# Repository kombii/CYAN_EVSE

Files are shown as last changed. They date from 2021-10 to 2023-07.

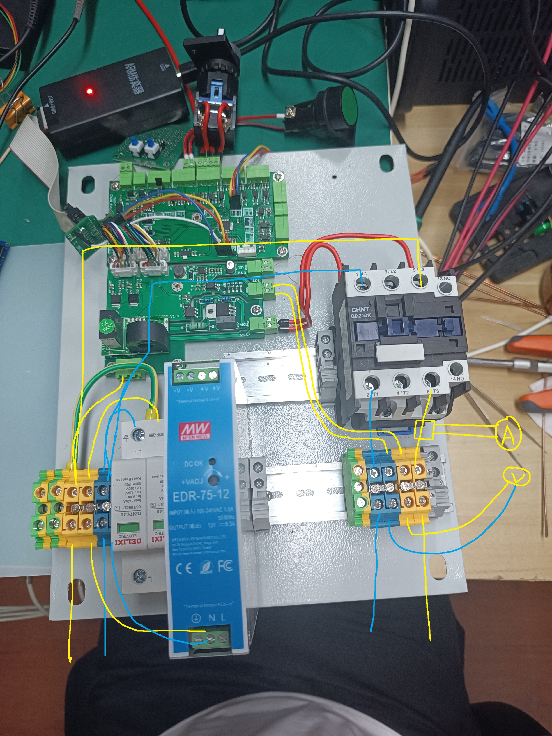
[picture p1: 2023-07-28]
Design/1.2配电 - 副本.jpg

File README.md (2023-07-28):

# CYAN_EVSE
是咱自己的电动小车的充电桩设计。  
## 主要特性
- 符合中国国标GB/T 18487.1-2015
- 按照国标规定的模式3，连接方式C进行设计
- 支持最大32A(7kW)充电模式
- 支持动态供电能力调节
- 过温度断电保护（依赖外部温控开关）
- 电气异常保护（过压、过流、欠压）
- 基于外置电表/计量芯片的准确电能统计
- 完整的保护和工业级组件  
- 支持定时充电，定电量充电
- 可手动指定调节充电电流
- 可实现无感解锁
## 进度  
这是一个进行中的项目，将要实现和完成的功能如下：  
 + 硬件功能
	+ 进行调试测试的原理图绘制✔
	+ 进行测试板的pcb绘制✔
	+ 进行测试板的pcb贴装✔
	+ 进行配电箱的试装✔
	+ 进行发布版本的原理图绘制
	+ 进行发布版本的PCB绘制
	+ 发布完成品
 + 软件功能
	+ 完成PWM和ADC底层驱动✔
	+ 完成电表通信实现✔
	+ 完成充电基础逻辑✔
	+ 完成外部锁定逻辑✔
	+ 完成紧急状态处理逻辑✔
	+ 软件联调和测试✔
## 碎碎念
 已经完成了试运行版本，还缺少定时启动的功能，不得不说有些车企的设计理念和用户需求完全不沾边啊。。。。。

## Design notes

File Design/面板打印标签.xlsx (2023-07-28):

警告 | 急停
市电接入 | 车辆连接 | 鉴权锁定
确定/菜单 | 充电启动 | 选择/±
警告 | 急停
市电接入 | 车辆连接 | 鉴权锁定
确定/菜单 | 充电启动 | 选择/±

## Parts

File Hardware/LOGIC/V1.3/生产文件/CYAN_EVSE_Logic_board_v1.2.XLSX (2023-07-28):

Comment | Designator | Footprint
10K | R1, R4, R5, R6 | 0805 | 4
4.7K | R2, R16, R21, R26, R33, R36, R39, R40, R44, R47 | 0805 | 10
120 | R3 | 1206 | 1
1K | R7, R10, R12, R15, R19, R24, R30 | 0805 | 7
1M | R8, R9, R11, R13, R17, R18, R22, R23, R27, R29, R34, R41, R45, R48 | 0805 | 14
100 | R14, R20, R25, R32, R35, R43, R46 | 0805 | 7
100K | R28, R37 | 0805 | 2
0 | R31, R49 | 0805 | 2
150K | R38 | 0805 | 1
39K | R42 | 0805 | 1
180 | R52 | 0805 | 1
1K | R54 | 1206 | 1
100nF 20V | C1, C2, C3, C4, C5, C8, C9, C12, C13, C16, C17, C18, C19, C20, C21, C22, C23, C25, C26, C27, C28, C30, C31 | 0805 | 23
1uF 20V | C6, C7, C24 | 0805 | 3
22pF 20V | C10, C14 | 0805 | 2
8.2pF 20V | C11, C15 | 0805 | 2
3.3nF 50V | C29 | 1206 | 1
SMBJ16CA | DR1 | SMB | 1
MAX3485 | IC1 | SOP8 | 1
TLP187 | IC2, IC5, IC7, IC8, IC10, IC11, IC12, IC13, IC14, IC15, IC16, IC18, IC19, IC20 | SOP6_4.6MM_W1.27_4PIN_N | 14
TLC372 | IC3 | SOP8 | 1
LMV358 | IC4, IC6 | SOP8 | 2
FOD8314 | IC9 | SOP6_7MM_WIDE_LEAD_N | 1
SI2302 | Q1, Q2, Q3, Q4, Q5 | SOT23-3 | 5
STM/GD32F103C8T6 | U1 | LQFP48 7X7 | 1
AMS1117-3V3 | V1 | SOT223 | 1
1N4148 | VD1, VD3 | SOD323 | 2
SMBJ6.8CA | VD2, VD4 | SMB | 2
8M 无源 | X1 | 3225 | 1
32.768khz 6pF 无源 | X2 | 3215 | 1
M3 | [NoValue], *1, *2, *3, *5 | M3 125X300 | 5
HDR-1X2 | J485R, JP4, JP8 | MC 1,5/ 2-G-3,81 | 3
HDR-1X6 | JP1, JP2 | XH2.54-6P | 2
HDR-1X4 | JP3, JP5, JP6, JP7, JP9, JP10, JP12 | MC 1,5/ 4-G-3,81 | 7
HDR-1X4 | JP11 | XH2.54-4P | 1
HDR-1X5 | JP13 | HDR-1X5 | 1
HDR-1X3 | JP14, JP15, JP16 | HDR-1X3 | 3
DS18B20 | IC17 | TO92A | 1
DEBUG PAD | TP1 | DEBUG PAD2 | 1

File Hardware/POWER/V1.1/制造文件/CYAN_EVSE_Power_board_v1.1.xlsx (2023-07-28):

Comment | Value | Voltage | Designator | Footprint | Quantity
C | 100nF | 25V | C1 | 0805 | 1
C | 100nf | 50V | C2, C3, C6, C15, C17, C19, C21 | 0805 | 7
C | 10uF | 50V | C4, C5, C14, C16, C18, C20 | 0805 | 6
C | 10uF | 25V | C7 | 0805 | 1
C | 10nf | 50V | C8 | 0805 | 1
C | 100nF | 20V | C9, C23 | 0805 | 2
X1 安规电容 | 10nf | 440V | CX2 | CX 10*13*11 | 1
C-CM | 220uf | 20V | E1 | CM D(6.3*5.4) | 1
BTA16_800 |  |  | IC1 | TO220B | 1
MOC3061 |  |  | IC2 | DIP6-300 | 1
PC817 |  |  | IC4 | SOP4-W2.54_M | 1
100uH |  |  | L2 | CD75 | 1
IM1281B |  |  | M2 | IM1281B | 1
S9014 |  |  | Q1 | SOT23-3N | 1
R | 16k |  | R1 | 0805 | 1
R | 1.8k |  | R3 | 0805 | 1
R | 10k |  | R6, R8 | 0805 | 2
R-CRR | 360 |  | R7, R10 | RS 1/2W | 2
R-CRR | 39 |  | R9 | RS 2W | 1
R | 180 |  | R11 | 0805 | 1
R | 51K |  | R13, R14, R15, R16 | 1206 | 4
R | 1M |  | R17 | 0805 | 1
TPS5430 |  |  | U1 | SOP8 | 1
7805 |  |  | V1 | TO252 | 1
7905 |  |  | V2 | TO252 | 1
B340AF-13 |  |  | VD1 | SMA | 1
FR107 |  |  | VD2 | SOD-123 | 1
M3 |  |  | *1, *2, *3, *5, *7 | M3 125X300 | 5
HDR-1X3 |  |  | JACIN | KF2EDGK5.0-3P_H | 1
HDR-1X2 |  |  | JACOUT, JDCIN, JMCOUT | MC 1,5/ 2-G-3,81 | 3
HDR-1X6 |  |  | JP1, JP2 | XH2.54-6P | 2

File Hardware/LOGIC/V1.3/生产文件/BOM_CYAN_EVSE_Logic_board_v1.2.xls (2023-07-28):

客户BOM清单 |  |  |  | 嘉立创用料信息
 |  |  |  | 匹配类型 | 匹配方式 | 匹配来源 | 顶层位号 | 顶层数 | 顶层贴装 | 底层位号 | 底层数 | 底层贴装 | 元件编号 | X-ray检查 | 贴装总数量 | 焊点总数量 | 焊点费小计 | 库类型 | 组装方式 | 元件名称 | 封装规格 | 最小起订数量 | 损耗数量 | 元器件来源 | 使用预订数量 | 工厂提供数量 | 工厂元件单价 | 工厂元件小计 | 收费原因
100nF20V | C1,C2,C3,C4,C5,C8,C9,C12,C13,C16,C17,C18,C19,C20,C21,C22,C23,C25,C26,C27,C28,C30,C31 | 0805 | 23 | 手动调整 | 手动替换 |  | C1, C2, C3, C4, C5, C8, C9, C12, C13, C16, C17, C18, C19, C20, C21, C22, C23, C25, C26, C27, C28, C30, C31 | 23 | 已贴装 |  | 0 | 未贴装 | C49678 | 不需要 | 115 | 230 | 2.30 | 基础库 | SMT贴片 | 100nF(104) ±10% 50V X7R | 0805 | 0 | 0 | 立创商城 | 0 | 115 | 0.0287 | 3.3005
150K | R38 | 0805 | 1 | 系统识别 | 自动匹配 |  | R38 | 1 | 已贴装 |  | 0 | 未贴装 | C17470 | 不需要 | 5 | 10 | 0.10 | 基础库 | SMT贴片 | 150KΩ (1503) ±1% | 0805 | 0 | 0 | 立创商城 | 0 | 5 | 0.0143 | 0.0715
1uF20V | C6,C7,C24 | 0805 | 3 | 系统识别 | 自动匹配 |  | C6, C7, C24 | 3 | 已贴装 |  | 0 | 未贴装 | C28323 | 不需要 | 15 | 30 | 0.30 | 基础库 | SMT贴片 | 1uF (105) ±10% 50V X7R | 0805 | 0 | 0 | 立创商城 | 0 | 15 | 0.0578 | 0.8670
SI2302 | Q1,Q2,Q3,Q4,Q5 | SOT23-3 | 5 | 手动调整 | 手动替换 |  | Q1, Q2, Q3, Q4, Q5 | 5 | 已贴装 |  | 0 | 未贴装 | C2891732 | 不需要 | 25 | 75 | 0.75 | 扩展库 | SMT贴片 | SI2302 | SOT-23-3 | 15 | 4 | 立创商城 | 0 | 29 | 0.1310 | 3.7990
4.7K | R2,R16,R21,R26,R33,R36,R39,R40,R44,R47 | 0805 | 10 | 系统识别 | 自动匹配 |  | R2, R16, R21, R26, R33, R36, R39, R40, R44, R47 | 10 | 已贴装 |  | 0 | 未贴装 | C17673 | 不需要 | 50 | 100 | 1.00 | 基础库 | SMT贴片 | 4.7KΩ (4701) ±1% | 0805 | 0 | 0 | 立创商城 | 0 | 50 | 0.0152 | 0.7600
22pF20V | C10,C14 | 0805 | 2 | 手动调整 | 手动替换 |  | C10, C14 | 2 | 已贴装 |  | 0 | 未贴装 | C1804 | 不需要 | 10 | 20 | 0.20 | 基础库 | SMT贴片 | 22pF (220) ±5% 50V C0G | 0805 | 0 | 0 | 立创商城 | 0 | 10 | 0.0708 | 0.7080
1K | R54 | 1206 | 1 | 系统识别 | 自动匹配 |  | R54 | 1 | 已贴装 |  | 0 | 未贴装 | C4410 | 不需要 | 5 | 10 | 0.10 | 基础库 | SMT贴片 | 1KΩ (1001) ±1% | 1206 | 0 | 0 | 立创商城 | 0 | 5 | 0.0238 | 0.1190
0 | R31,R49 | 0805 | 2 | 系统识别 | 自动匹配 |  | R31, R49 | 2 | 已贴装 |  | 0 | 未贴装 | C17477 | 不需要 | 10 | 20 | 0.20 | 基础库 | SMT贴片 | 0Ω (0R0) ±1% | 0805 | 0 | 0 | 立创商城 | 0 | 10 | 0.0138 | 0.1380
180 | R52 | 0805 | 1 | 系统识别 | 自动匹配 |  | R52 | 1 | 已贴装 |  | 0 | 未贴装 | C25270 | 不需要 | 5 | 10 | 0.10 | 基础库 | SMT贴片 | 180Ω (1800) ±1% | 0805 | 0 | 0 | 立创商城 | 0 | 5 | 0.0139 | 0.0695
10K | R1,R4,R5,R6 | 0805 | 4 | 系统识别 | 自动匹配 |  | R1, R4, R5, R6 | 4 | 已贴装 |  | 0 | 未贴装 | C17414 | 不需要 | 20 | 40 | 0.40 | 基础库 | SMT贴片 | 10KΩ (1002) ±1% | 0805 | 0 | 0 | 立创商城 | 0 | 20 | 0.0127 | 0.2540
1K | R7,R10,R12,R15,R19,R24,R30 | 0805 | 7 | 系统识别 | 自动匹配 |  | R7, R10, R12, R15, R19, R24, R30 | 7 | 已贴装 |  | 0 | 未贴装 | C17513 | 不需要 | 35 | 70 | 0.70 | 基础库 | SMT贴片 | 1KΩ (1001) ±1% | 0805 | 0 | 0 | 立创商城 | 0 | 35 | 0.0132 | 0.4620
1N4148 | VD1,VD3 | SOD323 | 2 | 系统识别 | 自动匹配 |  | VD1, VD3 | 2 | 已贴装 |  | 0 | 未贴装 | C2128 | 不需要 | 10 | 20 | 0.20 | 基础库 | SMT贴片 | 1N4148 | SOD-323F | 0 | 0 | 立创商城 | 0 | 10 | 0.0889 | 0.8890
1M | R8,R9,R11,R13,R17,R18,R22,R23,R27,R29,R34,R41,R45,R48 | 0805 | 14 | 手动调整 | 手动替换 |  | R8, R9, R11, R13, R17, R18, R22, R23, R27, R29, R34, R41, R45, R48 | 14 | 已贴装 |  | 0 | 未贴装 | C17514 | 不需要 | 70 | 140 | 1.40 | 基础库 | SMT贴片 | 1MΩ (1004) ±1% | 0805 | 0 | 0 | 立创商城 | 0 | 70 | 0.0139 | 0.9730
100K | R28,R37 | 0805 | 2 | 系统识别 | 自动匹配 |  | R28, R37 | 2 | 已贴装 |  | 0 | 未贴装 | C17407 | 不需要 | 10 | 20 | 0.20 | 基础库 | SMT贴片 | 100KΩ (1003) ±1%【停用，变更为C149504】 | 0805 | 0 | 0 | 立创商城 | 0 | 10 | 0.0144 | 0.1440
100 | R14,R20,R25,R32,R35,R43,R46 | 0805 | 7 | 系统识别 | 自动匹配 |  | R14, R20, R25, R32, R35, R43, R46 | 7 | 已贴装 |  | 0 | 未贴装 | C17408 | 不需要 | 35 | 70 | 0.70 | 基础库 | SMT贴片 | 100Ω (1000) ±1% | 0805 | 0 | 0 | 立创商城 | 0 | 35 | 0.0164 | 0.5740
AMS1117-3V3 | V1 | SOT223 | 1 | 系统识别 | 自动匹配 |  | V1 | 1 | 已贴装 |  | 0 | 未贴装 | C6186 | 不需要 | 5 | 20 | 0.20 | 基础库 | SMT贴片 | AMS1117-3.3 | SOT-223 | 0 | 0 | 立创商城 | 0 | 5 | 1.0711 | 5.3555
120 | R3 | 1206 | 1 | 系统识别 | 自动匹配 |  | R3 | 1 | 已贴装 |  | 0 | 未贴装 | C17909 | 不需要 | 5 | 10 | 0.10 | 基础库 | SMT贴片 | 120Ω(1200) ±1% | 1206 | 0 | 0 | 立创商城 | 0 | 5 | 0.0241 | 0.1205
39K | R42 | 0805 | 1 | 系统识别 | 自动匹配 |  | R42 | 1 | 已贴装 |  | 0 | 未贴装 | C25826 | 不需要 | 5 | 10 | 0.10 | 基础库 | SMT贴片 | 39KΩ (3902) ±1% | 0805 | 0 | 0 | 立创商城 | 0 | 5 | 0.0140 | 0.0700
<-以下为不贴装的元件->
LMV358 | IC4,IC6 | SOP8 | 2
SMBJ6.8CA | VD2,VD4 | SMB | 2
3.3nF50V | C29 | 1206 | 1
MAX3485 | IC1 | SOP8 | 1
8.2pF20V | C11,C15 | 0805 | 2
FOD8314 | IC9 | SOP6_7MM_WIDE_LEAD_N | 1
TLC372 | IC3 | SOP8 | 1
TLP187 | IC2,IC5,IC7,IC8,IC10,IC11,IC12,IC13,IC14,IC15,IC16,IC18,IC19,IC20 | SOP6_4.6MM_W1.27_4PIN_N | 14
SMBJ16CA | DR1 | SMB | 1
STM/GD32F103C8T6 | U1 | LQFP487X7 | 1
32.768khz6pF无源 | X2 | 3215 | 1
8M无源 | X1 | 3225 | 1
HDR-1X6 | JP1,JP2 | XH2.54-6P | 2
M3 | [NOVALUE],*1,*2,*3,*5 | M3125X300 | 5
HDR-1X3 | JP14,JP15,JP16 | HDR-1X3 | 3
HDR-1X5 | JP13 | HDR-1X5 | 1
HDR-1X4 | JP3,JP5,JP6,JP7,JP9,JP10,JP12 | HDR-1X4 | 7
HDR-1X2 | J485R,JP4,JP8 | MC1,5/2-G-3,81 | 3
HDR-1X4 | JP11 | HDR-1X4 | 1
DEBUGPAD | TP1 | DEBUGPAD2 | 1
DS18B20 | IC17 | TO92A | 1

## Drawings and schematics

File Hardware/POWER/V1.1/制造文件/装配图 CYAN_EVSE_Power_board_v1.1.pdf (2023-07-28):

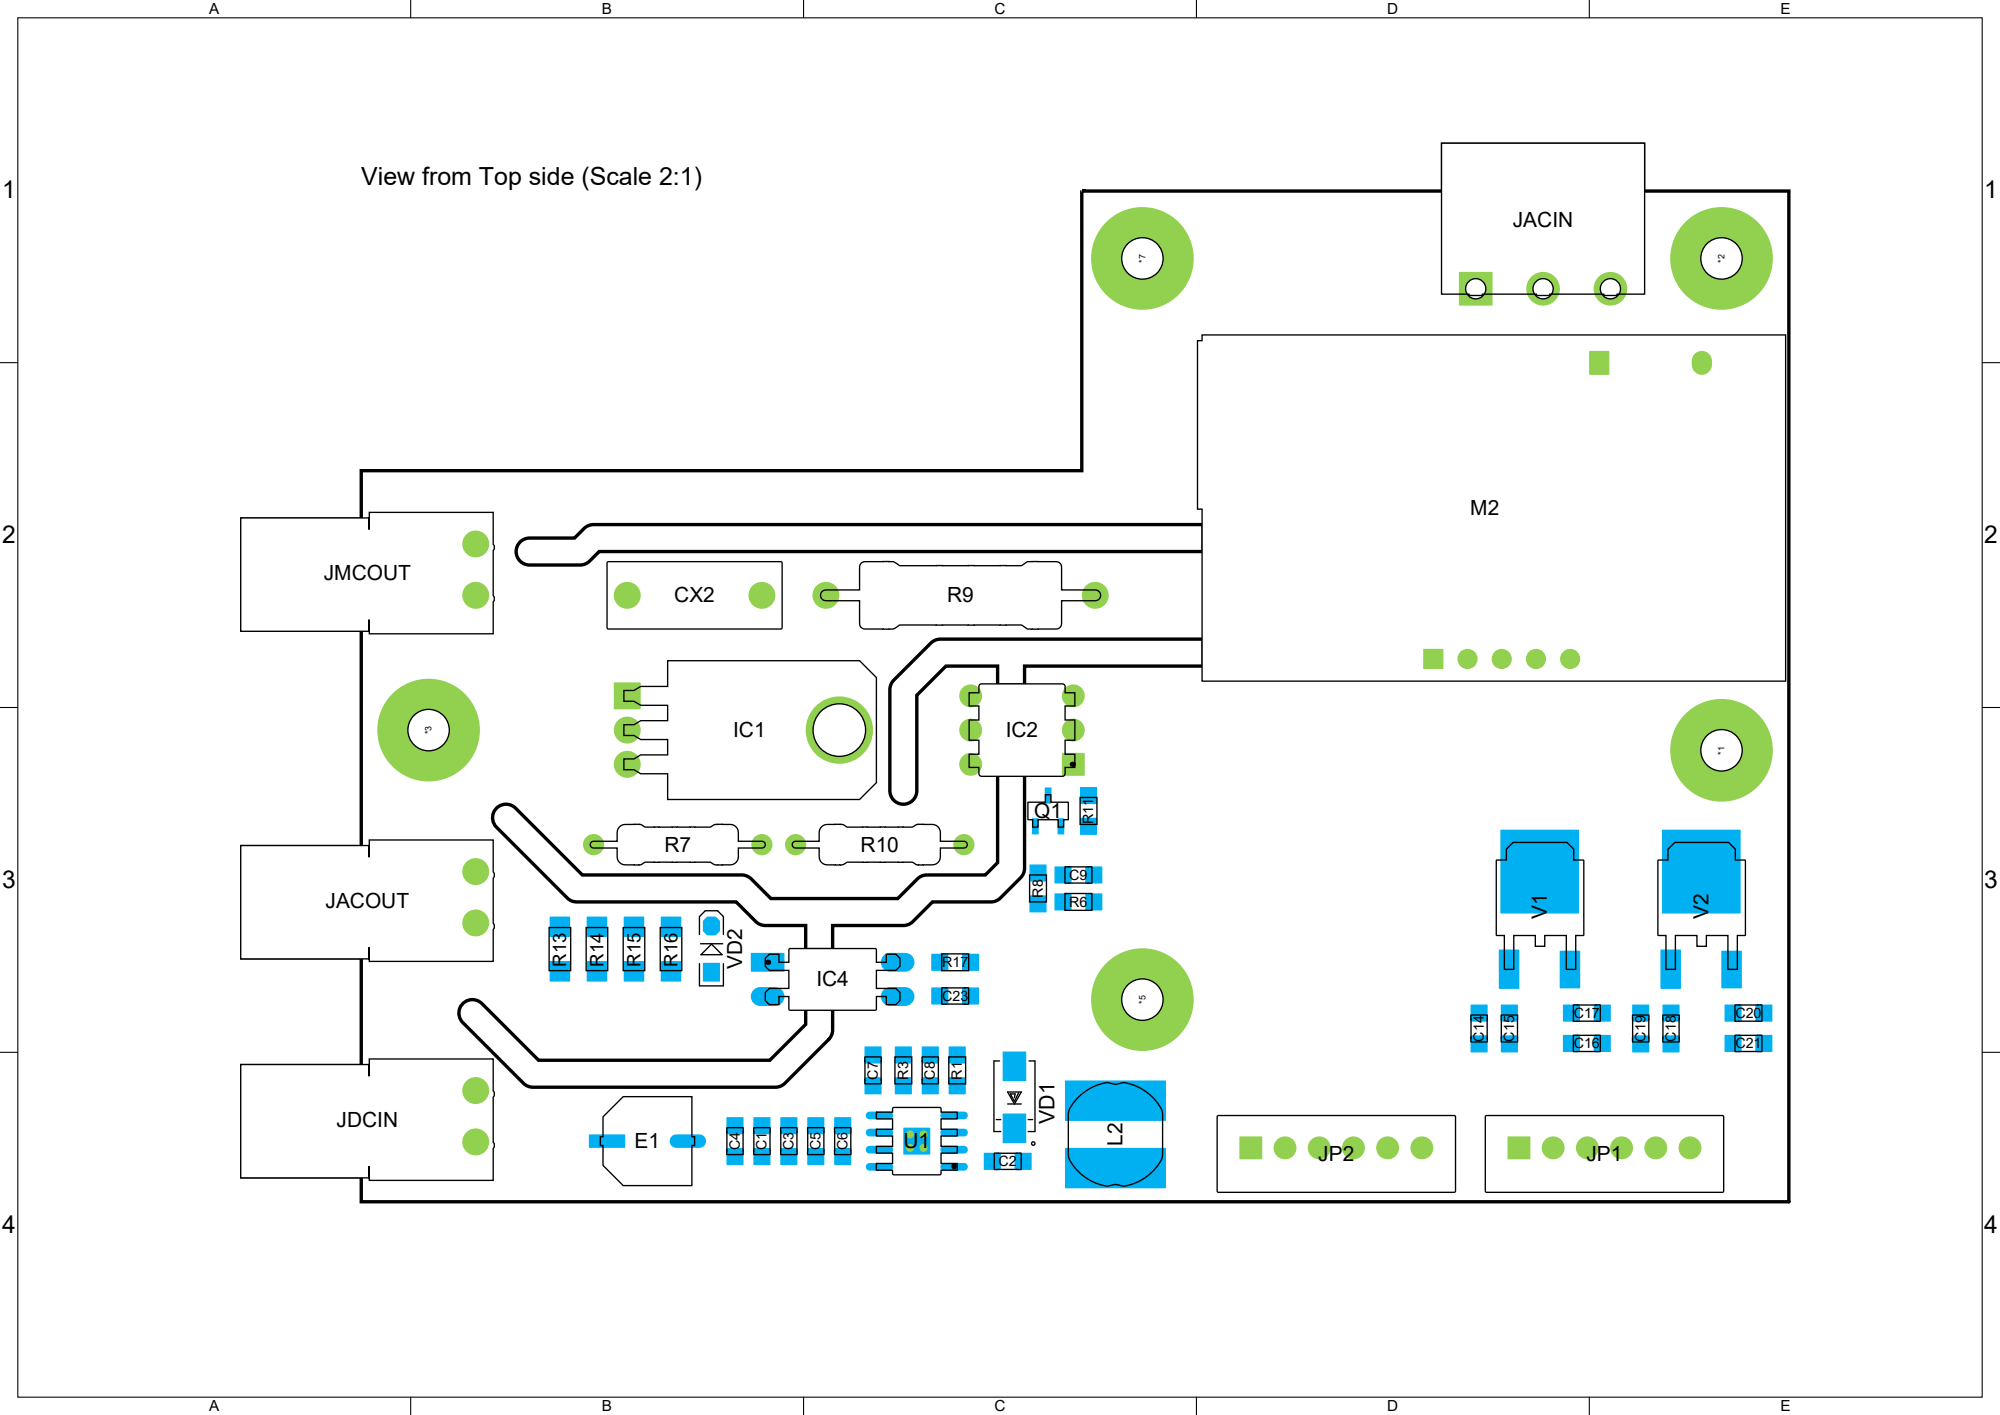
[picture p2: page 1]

View from Top side (Scale 2:1)

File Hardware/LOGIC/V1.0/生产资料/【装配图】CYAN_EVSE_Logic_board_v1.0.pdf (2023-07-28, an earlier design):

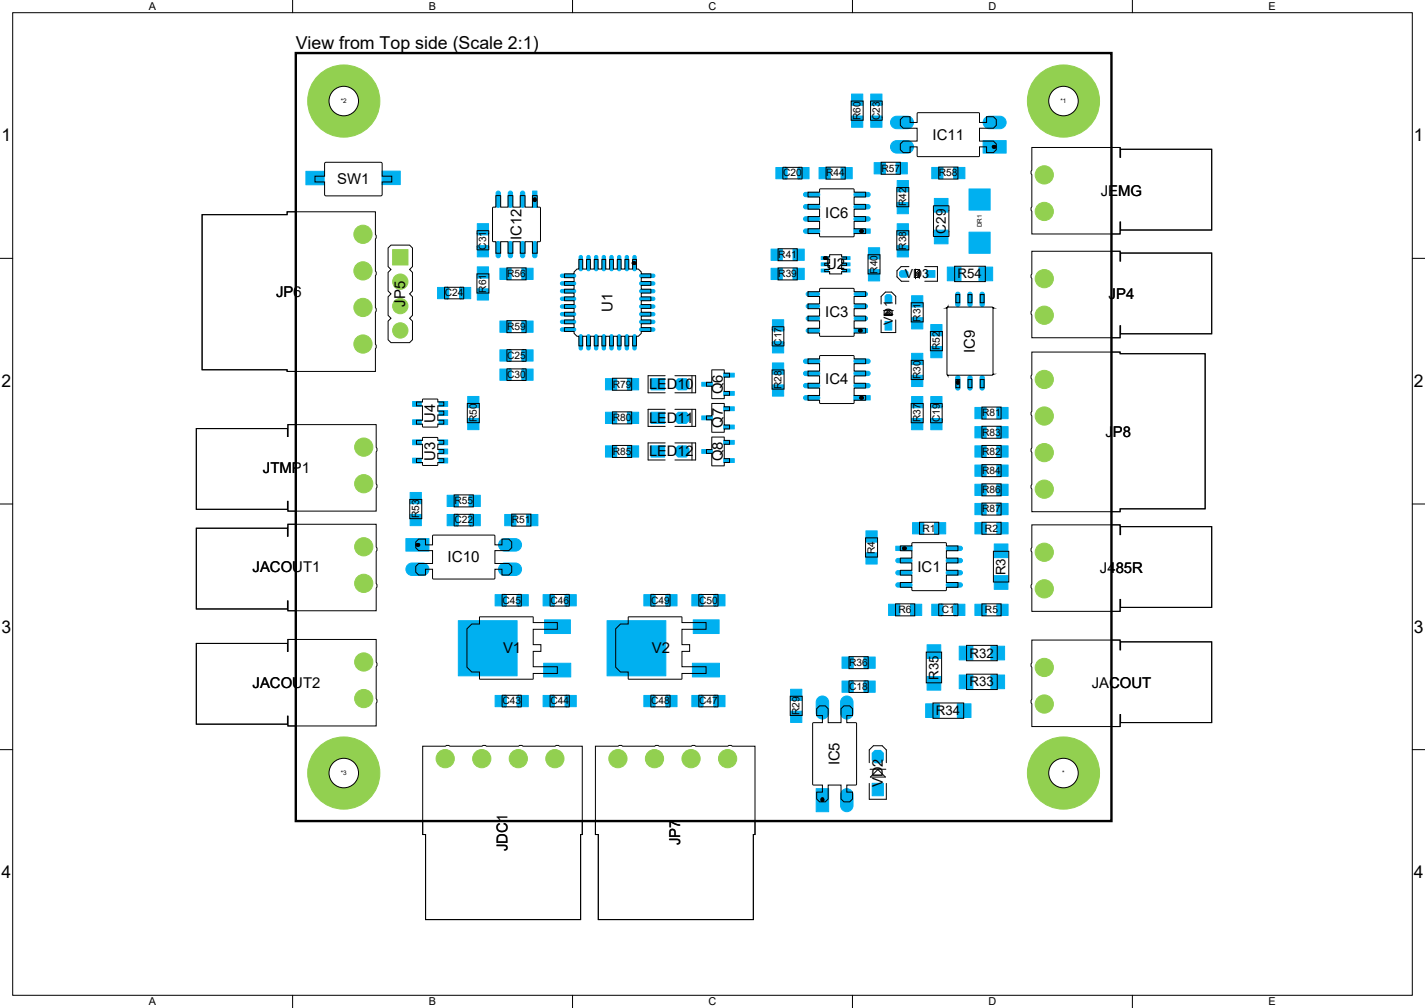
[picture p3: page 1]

View from Top side (Scale 2:1)

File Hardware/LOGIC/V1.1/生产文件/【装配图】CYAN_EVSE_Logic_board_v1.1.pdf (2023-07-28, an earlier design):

A

B

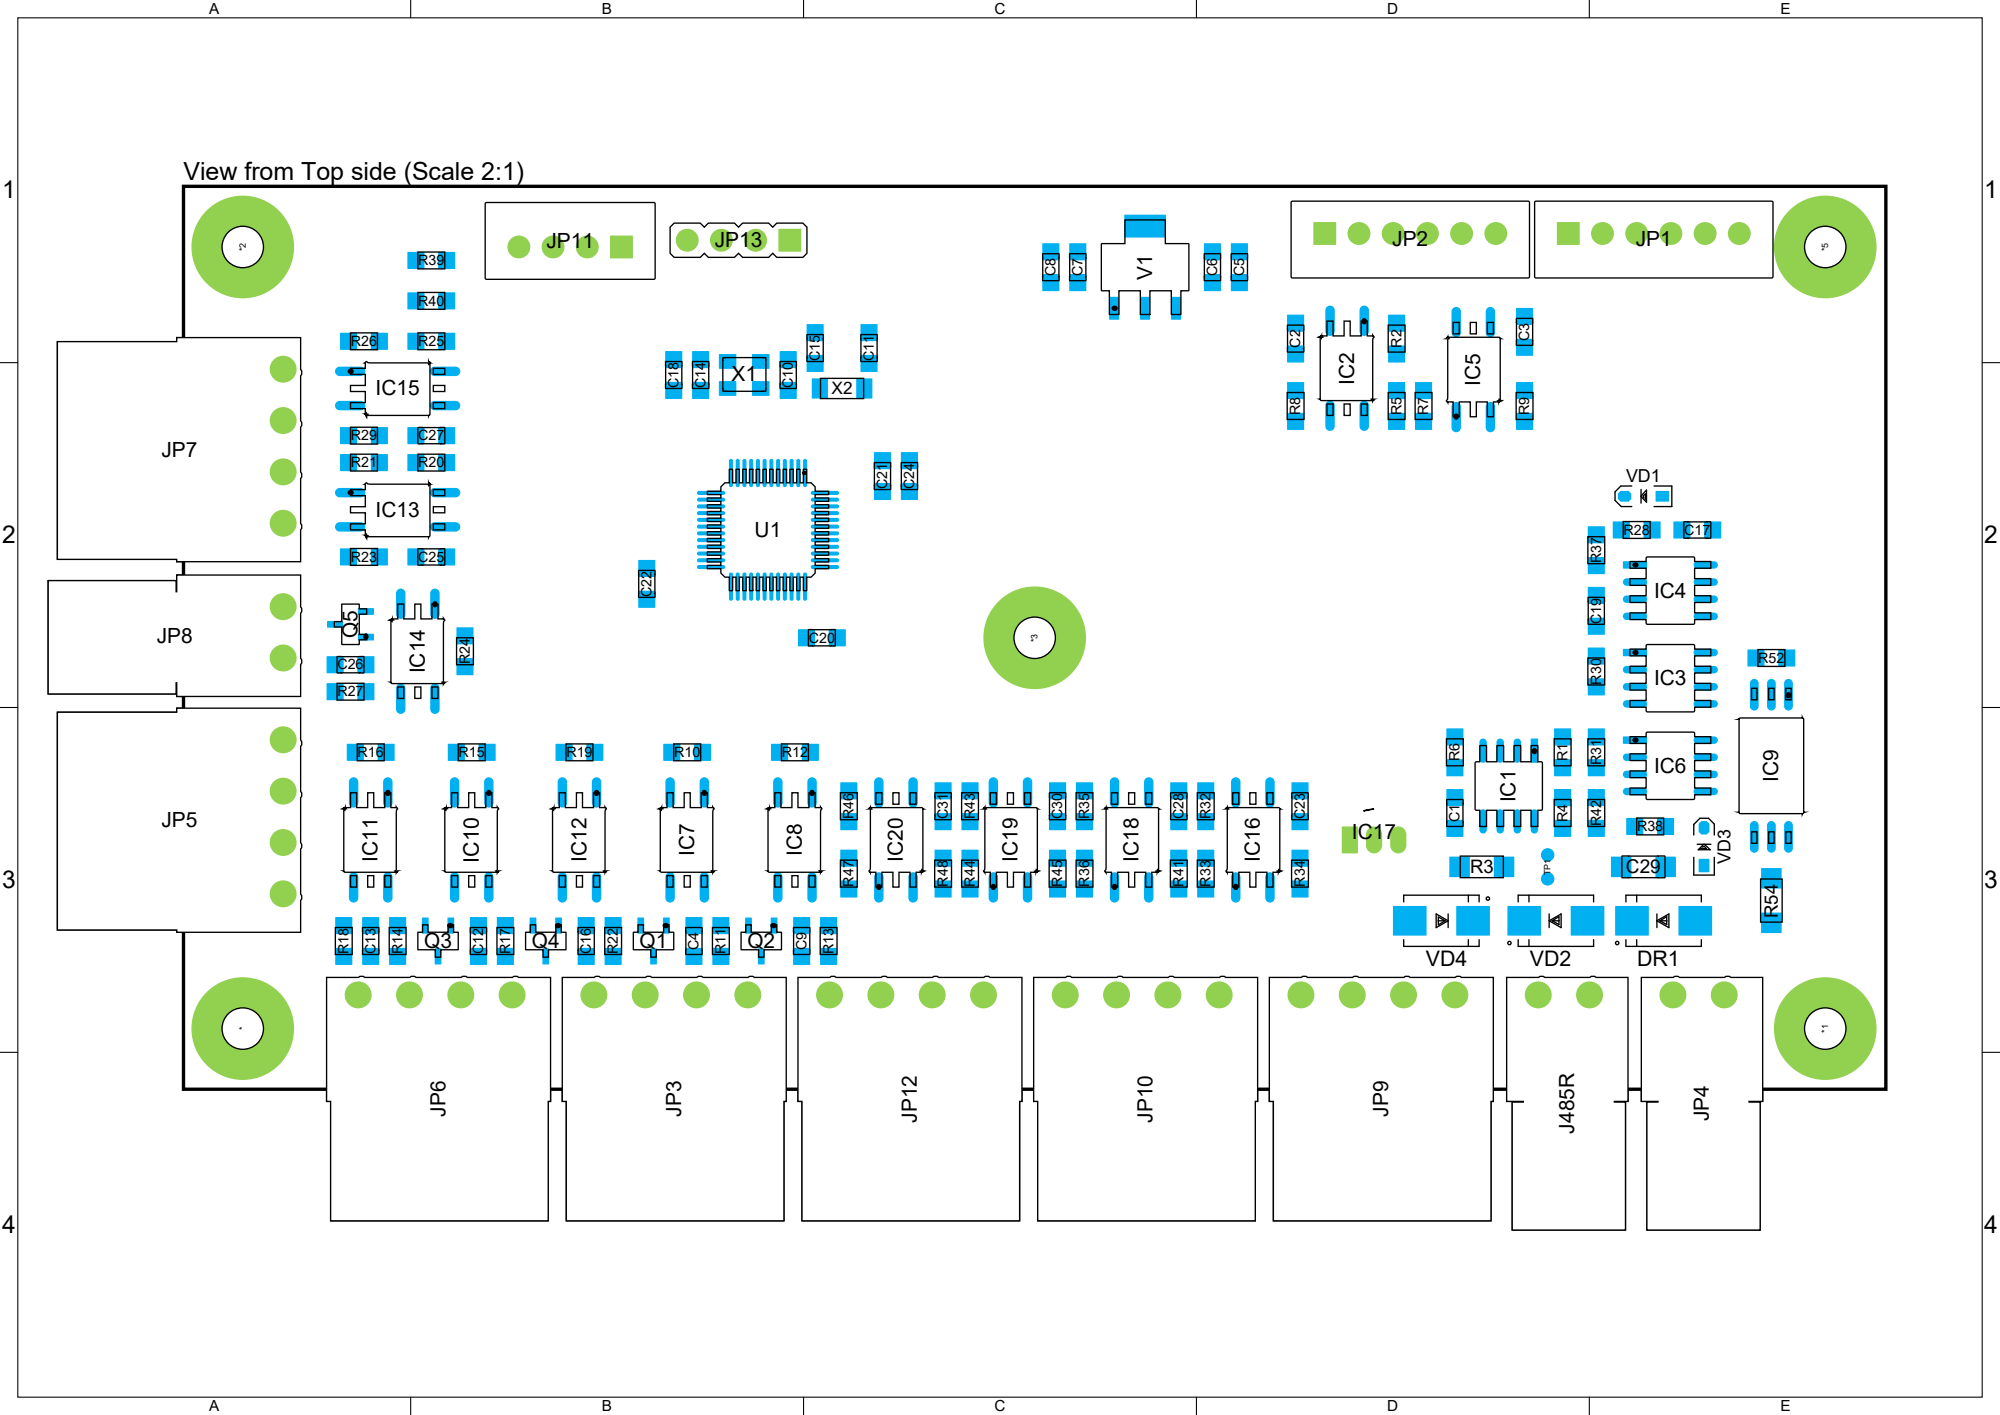
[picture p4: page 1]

View from Top side (Scale 2:1)

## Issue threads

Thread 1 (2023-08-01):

有几个问题和建议

gregrgr, 2023-08-01:
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
1、这样采集CP线电压，对CP线电压变化有影响，建议跟随采集后再处理信号。
2、后面那级RC滤波，对快速变化信号，时间太长，会导致动作时间不满足规范（家用无所谓）。
3、CP信号12V和MCU采集控制部分电路要分开，防雷安全性考虑。
4、-12可以不要，不影响通讯。

kombii, 2023-08-02:
这个项目居然有人回应:)
1.cp线对地（18487的方式3，r2和r3）阻抗是数个k欧，采集这边使用百k级的电阻分压，对于cp线的电压影响是比较小的，规范里对于pwm高电平电压的精度要求是10%左右，影响应该是不会导致兼容性问题的。
2.这个RC滤波的确会降低采样带宽，由于372这一级其实是个峰值保持电路（提取pwm高电平电压），这个延时不仅会体现在最后一级跟随之前，也会体现在这个保持电路上，这个电路在调试时经过测试，从12v转向0v（下降沿比上升要慢很多）需要40ms左右，规范里要求异常情况100ms内断开接触器，这个是可以满足的，不过电压采集的确可以再加速一些，未来会尝试调整。
3.很正确，现在的设计对于防雷这方面的确没有做很完善的设计，会考虑修改。
4.-12v调试时测试过，如果没有，对于大多数新车型都是可以充电的，只有一些比较老的车型，还有特斯拉进口型号会有兼容性问题，这个设计并没有带来太多成本问题，暂时先保留（实际上市面上很多便携充电枪和很大一部分第三方充电桩都没有-12v）

gregrgr, 2023-08-08:
我也在设计这个，所以你遇到的问题我也遇到过

Closed 2023-08-09.

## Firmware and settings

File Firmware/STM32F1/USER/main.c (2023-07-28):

#include "sys.h"
#include "usart.h"
#include "BspTime.h"
#include "delay.h"
#include "timer.h"
#include "state_mech.h"
#include "cp_signal.h"
#include "s1_switch.h"
#include "charge_current.h"
#include "ui.h"
#include "rtc.h"
#include "Ds64RomSearch.h"
#include "ds18b20.h"
#include "wdg.h"

//重启
void soft_reset(void)
{
	printf("#主控系统：系统即将（可控）重置，请关注原因！\r\n");
	printf("#---------------------------------------------------\r\n");
	// 关闭所有中断
    __set_FAULTMASK(1); 
	// 复位
	NVIC_SystemReset(); 
}

//检测温度传感器状态
void Check_DS(void){
	int32_t temperature;
	u8 i;
	u8 temp_checked = 0;
	Ds_RomSearch((GuidSearchTypdef *)DsGuid,8);
	if(Ds_Device_Searched_Num!=3){
		printf("#测温系统：测温传感器数量不足，拒绝启动:\r\n");
		while(1){
				EMG_OUT_GPIO_OUT = 1;
				delay_ms(100);
				EMG_OUT_GPIO_OUT = 0;
				delay_ms(100);
				if(EMG_STOP_GPIO_IN){
					soft_reset();
				}
		}
	}
	else{
		printf("#测温系统：测温传感器搜索结束，开始测试温度:\r\n");
		EMG_OUT_GPIO_OUT = 1;
		delay_ms(20);
		EMG_OUT_GPIO_OUT = 0;
		delay_ms(50);
		EMG_OUT_GPIO_OUT = 1;
		delay_ms(20);
		EMG_OUT_GPIO_OUT = 0;
		while(temp_checked==0){
			for(i=0;i<3;i++){
				DS18B20_Start(DsGuid[i].guid.u64Bits);
			}
			//delay_ms(1000);
			for(i=0;i<3;i++){
				temperature=DS18B20_Get_Temp_After_Start(DsGuid[i].guid.u64Bits);
				printf("#测温系统：传感器%d的温度读数是:%d",i,temperature);
				if(temperature>550){
					printf("!!!温度太高!!!\r\n");
					temp_checked = 0;
					delay_ms(500);
					break;
				}
				if(temperature==0){
					printf("!!!温度太低!!!\r\n");
					temp_checked = 0;
					delay_ms(500);
					break;
				}
				printf("\r\n");
				temp_checked = 1;
			}
		}
		printf("#测温系统：温度测试结果通过\r\n");
	}
}

//开机的时候检测应急按钮
void Power_On_Emg_Button(void){
	if(EMG_STOP_GPIO_IN){
		printf("#主控系统：开机时EMG按钮按下！\r\n");
	}
	while(EMG_STOP_GPIO_IN){
		EMG_OUT_GPIO_OUT = 1;
		delay_ms(100);
		EMG_OUT_GPIO_OUT = 0;
		delay_ms(500);
	}
}

int main(void)
{ 
	NVIC_PriorityGroupConfig(NVIC_PriorityGroup_2); //设置NVIC中断分组2:2位抢占优先级，2位响应优先级
	
	RCC_APB2PeriphClockCmd(RCC_APB2Periph_AFIO,ENABLE);
	GPIO_PinRemapConfig(GPIO_Remap_SWJ_JTAGDisable,ENABLE);
	
	State_Task_Init();
	
	uart1_init(4800);	 //到采集器
	uart2_init(115200);	 //485
	uart3_init(115200);	 //debug用
	
	init_bsptimer();
	delay_init();
	RTC_Init();
	DS18B20_Init();
	
	CP_Init();
	S1_Switch_Init();
	Get_Datas_From_EEPROM();
	Ui_System_Init();
	
	Power_On_Emg_Button();
	
	Check_DS();
	
	printf("#主控系统：系统自检通过，开始运行\r\n");
	
	IWDG_Init(4,625);    //与分频数为64,重载值为625,溢出时间为1s	
	
	while(1){
		main_task();
		IWDG_Feed();//喂狗
		if(EMG_STOP_GPIO_IN){
			soft_reset();
		}
	}
	
	
	
	
	
//	while(1){
//		if (USART2_RX_STA & 0x8000)
//		{
//			u16 len = USART2_RX_STA & 0x3fff; //得到此次接收到的数据长度
//			printf("收到包尾:\r\n");
//			uint16_t comp = (USART2_RX_BUF[0]-0x30)*100+(USART2_RX_BUF[1]-0x30)*10+(USART2_RX_BUF[2]-0x30);
//			printf("comp:%d\r\n",comp);
//			TIM_SetCompare1(TIM2,comp);
//			for (t = 0; t < len; t++)
//			{
//				USART_SendData(USART2, USART2_RX_BUF[t]); //向串口2发送数据
//				while (USART_GetFlagStatus(USART2, USART_FLAG_TC) != SET)
//					; //等待发送结束
//			}
//			printf("\r\n\r\n"); //插入换行
//			
//			
//			USART2_RX_STA = 0;
//		}
//		else
//		{
//			delay_ms(10);
//		}
//	}
	//		TIM_SetCompare2(TIM3,led0pwmval);
}

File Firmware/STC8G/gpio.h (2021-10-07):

#ifndef	__GPIO_H
#define	__GPIO_H

#include	"config.h"

#define	GPIO_PullUp		0	//上拉准双向口
#define	GPIO_HighZ		1	//浮空输入
#define	GPIO_OUT_OD		2	//开漏输出
#define	GPIO_OUT_PP		3	//推挽输出

#define	GPIO_Pin_0		0x01	//IO引脚 Px.0
#define	GPIO_Pin_1		0x02	//IO引脚 Px.1
#define	GPIO_Pin_2		0x04	//IO引脚 Px.2
#define	GPIO_Pin_3		0x08	//IO引脚 Px.3
#define	GPIO_Pin_4		0x10	//IO引脚 Px.4
#define	GPIO_Pin_5		0x20	//IO引脚 Px.5
#define	GPIO_Pin_6		0x40	//IO引脚 Px.6
#define	GPIO_Pin_7		0x80	//IO引脚 Px.7
#define	GPIO_Pin_All	0xFF	//IO所有引脚
	
#define	GPIO_P0			0		//
#define	GPIO_P1			1
#define	GPIO_P2			2
#define	GPIO_P3			3
#define	GPIO_P4			4
#define	GPIO_P5			5
#define	GPIO_P6			6
#define	GPIO_P7			7


typedef struct
{
	u8	Mode;		//IO模式,  		GPIO_PullUp,GPIO_HighZ,GPIO_OUT_OD,GPIO_OUT_PP
	u8	Pin;		//要设置的端口	
} GPIO_InitTypeDef;

u8	GPIO_Inilize(u8 GPIO, GPIO_InitTypeDef *GPIOx);

#endif

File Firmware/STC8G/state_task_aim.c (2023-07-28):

#include "state_mech.h"
#include "gpio.h"
#include "dlt645.h"
#include "charge_current.h"
#include "BspTime.h"
#include "cp_signal.h"
#include "s1_switch.h"
#include "uart.h"

uint16_t bdata statemech = 0;

sbit emgstate			=statemech^0;
sbit outputen			=statemech^1;
sbit lock				=statemech^2;
sbit output				=statemech^3;

sbit sw_error			=statemech^4;
sbit overtemp			=statemech^5;
sbit overvoltage		=statemech^6;
sbit undervoltage		=statemech^7;

sbit overcurrent		=statemech^8;
sbit emgstop			=statemech^9;
sbit chargegun			=statemech^10;
sbit chargestart		=statemech^11;

sbit S1_Switch_State	=statemech^12;
sbit rfidlock			=statemech^13;
sbit blelock 			=statemech^14;
sbit outvol 			=statemech^15;

uint32_t cp_voltage = 0;//cp线电压，以0.01v单位
uint8_t charge_state = 0;//充电状态
uint8_t cp_state = 0;//cp线档位
uint8_t stop_reason = 0;//停止原因
uint16_t avaliable_current = 0;//当前电流
//1;//过压
//2;//过流
//3;//车主动断开
//4;//充电期间直接拔枪
//5;//应急开关
//6;//过热
//7;//接触器输出错误
//255;//未知

void State_Task_Init(void){
	GPIO_InitTypeDef	GPIO_InitStructure;
	GPIO_InitStructure.Pin  = GPIO_Pin_3;
	GPIO_InitStructure.Mode = GPIO_HighZ;
	GPIO_Inilize(GPIO_P3,&GPIO_InitStructure);	//33 EMG总输入 
	GPIO_InitStructure.Pin  = GPIO_Pin_3|GPIO_Pin_2|GPIO_Pin_1|GPIO_Pin_0;
	GPIO_InitStructure.Mode = GPIO_HighZ;
	GPIO_Inilize(GPIO_P2,&GPIO_InitStructure);	//23 输出电压检测 22 21 20 外部输入信号
	GPIO_InitStructure.Pin  = GPIO_Pin_6|GPIO_Pin_5;
	GPIO_InitStructure.Mode = GPIO_HighZ;
	GPIO_Inilize(GPIO_P3,&GPIO_InitStructure);	//36 温度错误 35 应急停止
	GPIO_InitStructure.Pin  = GPIO_Pin_4;
	GPIO_InitStructure.Mode = GPIO_OUT_PP;
	GPIO_Inilize(GPIO_P3,&GPIO_InitStructure);	//34 接触器输出
	
	//GPIO_InitStructure.Pin  = GPIO_Pin_0;
	//GPIO_InitStructure.Mode = GPIO_OUT_PP;
	//GPIO_Inilize(GPIO_P2,&GPIO_InitStructure);	//20 指示输出
	P34 = 0;
	
	//初始化sbit变量
	emgstate = 0;//紧急状态输入 1紧急 0正常
	outputen = 0;//输出允许 1允许 0不允许
	lock = 1;//外部锁定系统 1锁定 0解锁
	output = 0;//输出 1输出 0关闭输出
	sw_error = 0;//软件错误标记 1错误 0正常
	overtemp = 0;//过温 1紧急 0正常
	overvoltage = 0;//过压 1紧急 0正常
	undervoltage = 0;//欠压 1紧急 0正常
	overcurrent = 0;//过流 1紧急 0正常
	emgstop = 0;//紧急停止按钮 1紧急 0正常
	chargegun = 0;//插枪状态 1插入 0拔出
	chargestart = 0;//充电启动过的状态 1启动过了 0没有
	rfidlock = 1;//rfid锁定系统 1锁定 0解锁
	blelock = 1;//ble锁定系统 1锁定 0解锁
	outvol = 0;//输出电压状态
}

//硬件紧急输入采集
void HW_EMG_Task(void){
	emgstate = !P33; 	//NOR输出，低有效
	emgstop = P35; 		//光偶上拉输出 高有效
	overtemp = P36;		//光偶上拉输出 高有效
}
//输出状态
void Out_Task(void){
	if(	(outputen) 	 && 
		!(emgstate) && 
		!(emgstop) &&
	    !(overtemp)
	) output = 1;
	else output = 0;
	P34 = output;
	outvol = P23;
	PrintString1("^");
	WriteData1((uint8_t *)&statemech,2);
	WriteData1((uint8_t *)&stop_reason,1);
	WriteData1((uint8_t *)&avaliable_current,2);
	PrintString1("&\r\n");
}
//采集电压任务
void Elec_Vol_Task(void){
	//判断电压状态
	if((*(float *)elec_condition.Voltage) > ac_voltage_max)
	{
	overvoltage = 1;
	}
	else {
		overvoltage = 0;
		if ((*(float *)elec_condition.Voltage) < ac_voltage_min && !(((*(float *)elec_condition.Voltage)>=-EPSINON) && ((*(float *)elec_condition.Voltage)<=EPSINON)))
		{
		undervoltage = 1;
		}
		else 
		{
		undervoltage = 0;
		}	
	}
}

//采集电流任务
void Elec_Curr_Task(void){
	//判断电流状态
	static autotimer *Overcurrenttimer = NULL;
	if(avaliable_current > 200)
	{//20a以上用ac_current_size_20判断，1.1倍
		if((*(float *)elec_condition.Current) > (ac_current_size_20*avaliable_current/10))
		{//大于值，申请定时器，开始计时
			if(Overcurrenttimer == NULL)
			{
				Overcurrenttimer = obtainTimer(0);
			}
			if(!IS_TIMEOUT_1MS(Overcurrenttimer,5000)){
				returnTimer(Overcurrenttimer);
				Overcurrenttimer = NULL;
				overcurrent = 1;
			}
		}
		else
		{
			if(Overcurrenttimer != NULL)
			{
				Overcurrenttimer = obtainTimer(0);
			}
			overcurrent = 0;
		}	
	}
	else
	{//20a以下用ac_current_size_0判断 +2a
		if((*(float *)elec_condition.Current) > (ac_current_size_0+(avaliable_current/10L)))
		{//大于值，申请定时器，开始计时
			if(Overcurrenttimer == NULL)
			{
				Overcurrenttimer = obtainTimer(0);
			}
			if(!IS_TIMEOUT_1MS(Overcurrenttimer,5000)){
				returnTimer(Overcurrenttimer);
				Overcurrenttimer = NULL;
				overcurrent = 1;
			}
		}
		else
		{
			if(Overcurrenttimer != NULL)
			{//刚从过流恢复
				returnTimer(Overcurrenttimer);
				Overcurrenttimer = NULL;
			}
			overcurrent = 0;
		}	
	}
}
//充电任务，负责整个充电管理
void Charge_task(void){
	static autotimer *stoppingtimer = NULL;//停止计时器
	static autotimer *connecttimer = NULL;//接触器粘连计时器
	switch(charge_state){
	case charge_state_idle:
		{
			if(cp_state == 12){
				//状态1下检测到12v电压则挺正常的，啥都不用干
				S1_Switch_Off();//s1切换到12v
				chargestart = 0;//设置未启动状态
				if(outvol == 1&& connecttimer == NULL){
					connecttimer = obtainTimer(0);//取一个定时器，设置时间0
				}
				else if(outvol == 1 && connecttimer != NULL){
					if(!IS_TIMEOUT_1MS(connecttimer,2000))
					{//到2s电压都没有掉下去，是错误状态
						returnTimer(connecttimer);//计时器没用了
						connecttimer = NULL;
						charge_state = charge_state_err;//进入0
					}
				}
				else if(outvol == 0 && connecttimer == NULL){
					//0是正常状态，并且无需计时器
				}
				else if(outvol == 0 && connecttimer != NULL){
					returnTimer(connecttimer);//计时器没用了
					connecttimer = NULL;
				}
			}
			else if(cp_state == 9){
				//状态1下检测到9v电压则意味着插枪
				PrintString1("#gun insert\r\n");
				chargegun = 1;//设置插枪
				charge_state = charge_state_insert_gun;
			}
			else if(cp_state == 6){
			}
			else{
				//charge_state = charge_state_err;//进入0
			}
			break;
		}
	case charge_state_insert_gun:
		{
			//状态2下检测到12v电压则意味着拔枪
			if(cp_state == 12){
				PrintString1("#gun pull out\r\n");
				S1_Switch_Off();//s1切换到12v
				chargegun = 0;//设置拔枪
				rfidlock = 1;//返回时上锁
				charge_state = charge_state_idle;
			}
			//状态2下,自检如果通过，那么开始输出pwm
			else if(cp_state == 9){
				//lock解锁状态，那么打开pwm，继续运行
				if(lock == 0&&!(emgstate) && chargestart == 0)
				{
					PrintString1("#self test ok\r\n");
					S1_Switch_On();//s1切换到pwm
					charge_state = charge_state_gun_pwm;
					chargestart = 1;//设置已经经历过插枪检测过程，不拔出不允许再次启动
					stop_reason = 0;//重新插枪了，清理停止原因
				}
				else{
					//什么都不做，让车子等
				}
			}
			else if(cp_state == 6){
				//状态2下,如果稳定6v,存在问题,需要处理
				//charge_state = charge_state_err;//进入0
			}
			else{
				//charge_state = charge_state_err;//进入0
			}
			break;
		}
	case charge_state_gun_pwm:
		{
			//状态2'下检测到12v电压则意味着拔枪
			if(cp_state == 12){
				PrintString1("#gun pull out(pwm)\r\n");
				chargegun = 0;//设置拔枪
				charge_state = charge_state_nogun_pwm;
			}
			else if(cp_state == 9){
				//状态2'下检测到9v电压则意味着一切正常
			}
			//状态2'下检测到6v电压则意味着ev准备好
			else if(cp_state == 6){
				//lock解锁状态，那么打开pwm，继续运行
				if(lock == 0&&!(emgstate))
				{
					PrintString1("#ev ok power on\r\n");
					outputen = 1;//启用电能输出
					charge_state = charge_state_charging;
				}
				else{
					//什么都不做，让车子等
				}
			}
			else
			{
				//charge_state = charge_state_err;//进入0
			}
			break;
		}
	case charge_state_charging:
		{
			//状态3'下检测到12v电压则意味着拔枪
			if(cp_state == 12){
				PrintString1("#gun pull out(charging)\r\n");
				stop_reason = 4;//充电期间直接拔枪
				chargegun = 0;//设置拔枪
				outputen = 0;//关闭电能输出（可能带载）
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

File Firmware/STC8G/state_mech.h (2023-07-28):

#ifndef	__STATE_MECH_H
#define	__STATE_MECH_H
#include "TYPESS.H"
//状态机们-----------------------------------------

#define ac_voltage_max (260.00f)
#define ac_voltage_min (180.00f)

#define ac_current_size_20 (1.1f)
#define ac_current_size_0 (2.0f)

#define EPSINON (1e-6)

extern bit emgstate;//紧急状态输入 1紧急 0正常
extern bit outputen;//输出允许 1允许 0不允许
extern bit lock;//外部锁定系统 1锁定 0解锁

extern bit output;//输出 1输出 0关闭输出

extern bit overtemp;//过温 1紧急 0正常
extern bit overvoltage;//过压 1紧急 0正常
extern bit undervoltage;//欠压 1紧急 0正常
extern bit overcurrent;//过流 1紧急 0正常
extern bit emgstop;//紧急停止按钮 1紧急 0正常

extern bit chargegun;//插枪状态 1插入 0拔出
extern bit chargestart;//充电启动过的状态 1启动过了 0没有

extern bit S1_Switch_State;//S1开关状态
extern bit rfidlock;//rfid锁状态
extern bit blelock;//ble锁状态
extern bit outvol;//输出电压状态

extern uint32_t cp_voltage;//cp线电压，以0.01v单位
extern uint8_t charge_state;//充电状态
extern uint8_t cp_state;//cp线档位
extern uint16_t avaliable_current;//当前电流
//0 6 9 12 255

typedef enum _charge_states{
	charge_state_idle,//状态1
	charge_state_insert_gun,//状态2
	charge_state_gun_pwm,//状态2‘
	charge_state_charging,//状态3’
	charge_state_stopping,//状态3
	charge_state_nogun_pwm,//状态1‘
	charge_state_err//状态0
}charge_states;

void State_Task_Init(void);
void main_task(void);

#endif

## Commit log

2021-10-07 开始使用git
    已经完成了测试板和部分程序
    [CYAN_EVSE_Logic_board_v1.0.PrjPcb, CYAN_EVSE_Logic_board_v1.0.SchDoc, 计量芯片版本.SchDoc]
2021-10-08 实现了CP信号采集相关代码
2021-10-08 串口重新定义到P1617,方便调试
2021-10-08 删掉了测试警告的函数未使用变量
2021-10-08 状态机引用类型定义
2021-10-08 添加了S1开关的处理代码
2021-10-08 delay改为1ms计数
2021-10-08 添加了操作pwm启用禁用的函数，并且默认初始化后不启动pwn
2021-10-09 实现了设置充电桩可提供功率的功能
2021-10-09 修正了一些拼写，为cp信号模块添加了初始化函数
2021-10-09 修正了一些拼写
2021-10-09 添加了true和false的定义
2021-10-11 添加了电流寄存器
2021-10-11 添加cp信号adc引脚初始化
2021-10-11 修复了0指令的错误bug
2021-10-11 添加了电压电流判断阈值
2021-10-11 添加了各种任务函数独立提取
2021-10-11 添加了串口引脚初始化
2021-10-11 添加了cp引脚初始化
2023-07-28 基本完成了试运行版本，进行了数个版本迭代
    [BOM CYAN_EVSE_Logic_board_v1.2.xls, BOM_CYAN_EVSE_Logic_board_v1.2.xls, CYAN_EVSE_Logic_board_v1.0.PrjPcb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]
